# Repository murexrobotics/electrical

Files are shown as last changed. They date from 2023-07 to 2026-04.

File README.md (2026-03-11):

# MUREX Electrical

Attempt the impossible.

## Welcome!

Welcome to MUREX Robotics Electrical. We are focused on pushing boundaries and making electronics/systems design more accessible to all.

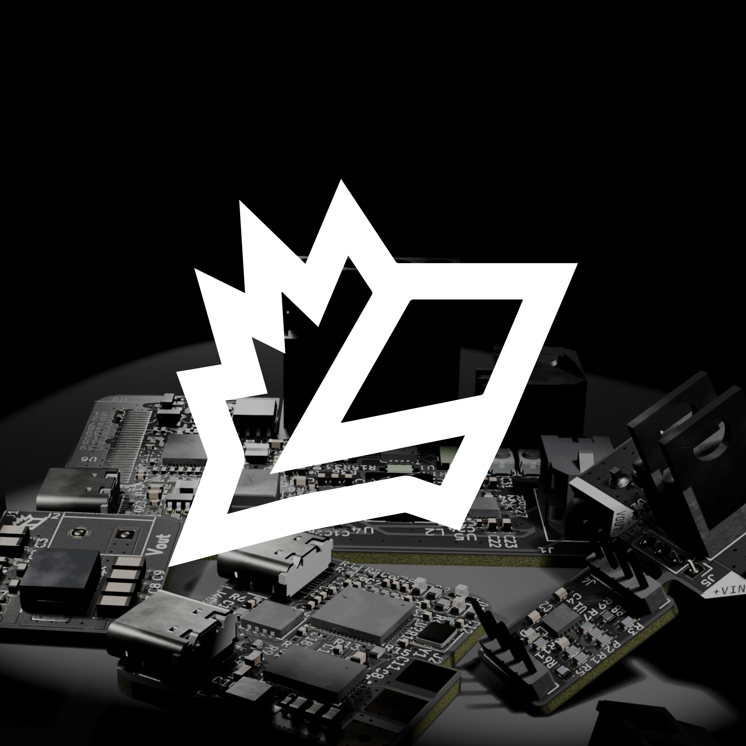
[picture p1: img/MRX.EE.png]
Cover Image


## Introduction

> *"I do not think there is any thrill that can go through the human heart like that felt by the inventor as he sees some creation of the brain unfolding to success"*
– [Nikola Tesla](https://en.wikipedia.org/wiki/Nikola_Tesla)

MUREX Robotics Electrical focuses on making everything highly integrated and custom. We make industrial/commercial level motion, power, communication, vision and wireless systems accessible to all. By making components fully custom, we can accomplish unprecedented levels of integration within MUREX robotics systems. By keeping COTS parts to a minimum, we vertically integrate all aspects of the robot, minimize space, and surprisingly, minimize cost. We don't do it the easy way. That's not what we believe in.

## Attempt the Impossible

Going to back our "mission statement"... (it's not really a mission statement, more a motivational quote)

> *Attempt the impossible*

What does this mean? Now that you have read through what MUREX Robotics Electrical (or *elec*) is all about and equipped with technical expertise, we can finally say what the true meaning is.

***Attempt the impossible***: We do it the best way possible. If pre-built parts or breakout boards don't cut it, we don't use it. If a processor isn't powerful enough, we don't use it. If a board isn't small enough, we make it smaller. No matter how difficult it may be to accomplish, we will follow through. No matter how hard it is. Things don't always go your way. No matter how hard you try to perfect your schematic, your PCB layout, your system integration, it still might not work out. Things are bound to go wrong, and it is up to *us* do it right. It's "impossible", a non-MUREX Robotics Electrical member might say. However, we accept it as the process. In the end, we will have achieved something others might have called "impossible". But the achievement only comes through endless, motivated attempts at the impossible.

> *Think Different*\
> *Unleash Innovation*\
> *Do It Right*

*Always attempting the impossible,*\
Members:

- Max Liu '26 (@xamuil2)
- Crane Lee '27 (@Crane-Lee)
- Osbert Chang '27 (@Osbertchang)
- Andrew Chen '28

Emeriti:

- Byran Huang '25 (@Hello9999901)
- Altan Unver '25 (@L0ad1n6)
- Varit Asavathiratham '25 (@BaritoDespacito)
- Chaney Hollis '23 (@chaneyhollis)

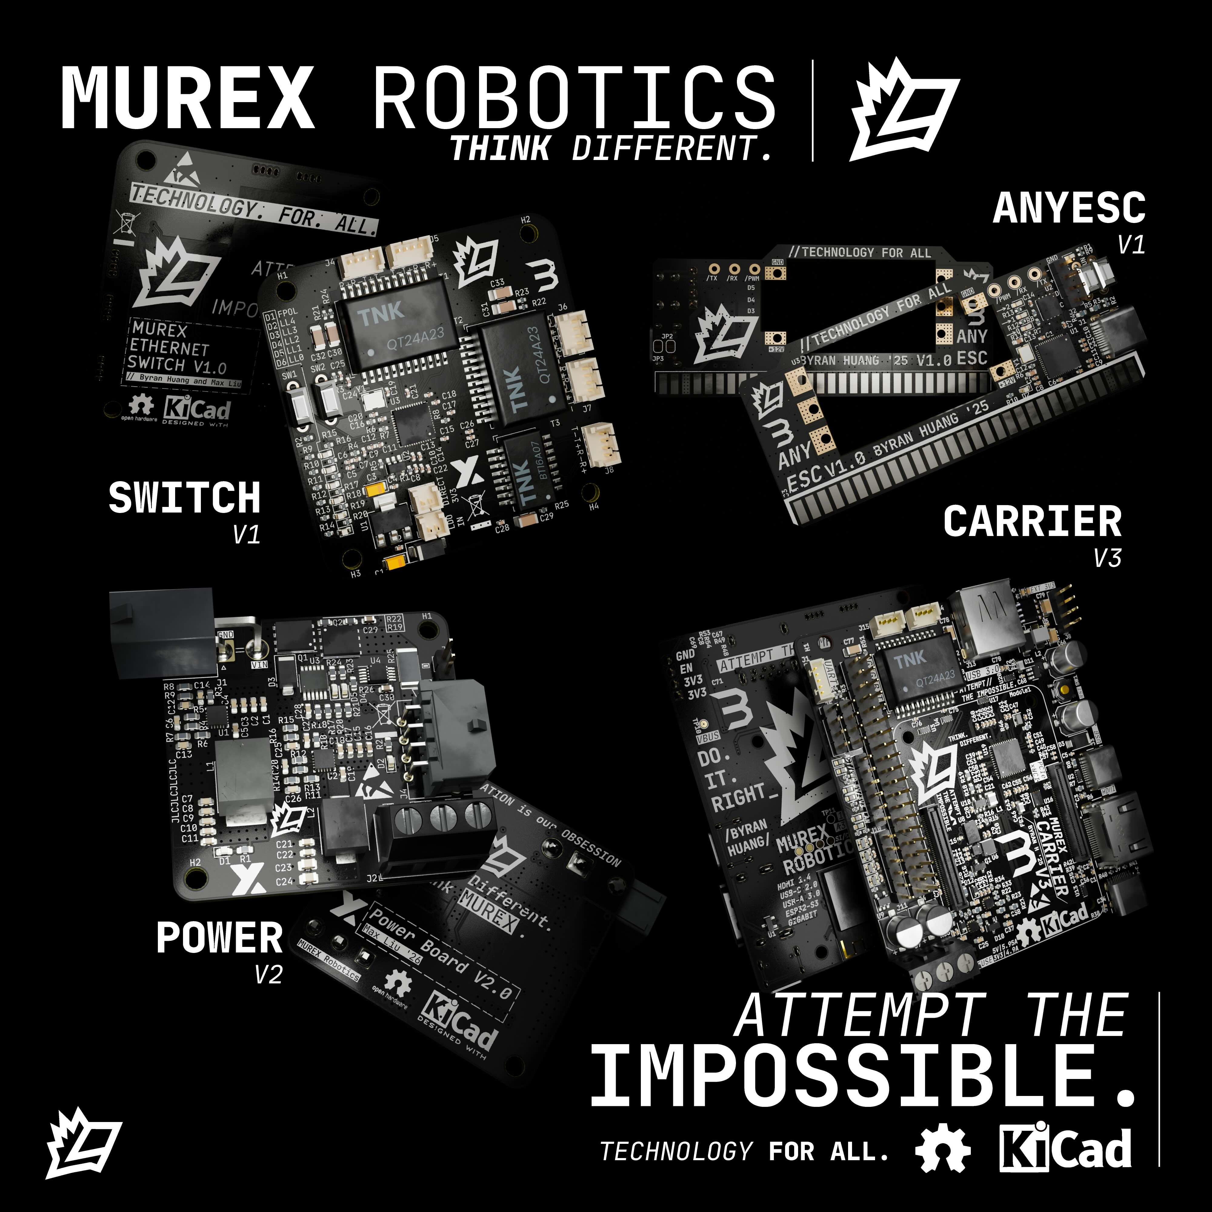
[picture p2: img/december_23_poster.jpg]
Raytraced Render

> December 2023 progress poster

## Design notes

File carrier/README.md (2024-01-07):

# Documentation

<https://docs.murexrobotics.com/elec/boards/carrier>

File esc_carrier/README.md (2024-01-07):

# Documentation

<https://docs.murexrobotics.com/elec/boards/esc_carrier>

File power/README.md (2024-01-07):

# Documentation

<https://docs.murexrobotics.com/elec/boards/power>

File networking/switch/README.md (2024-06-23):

# Documentation

<https://docs.murexrobotics.com/elec/boards/networking/switch>

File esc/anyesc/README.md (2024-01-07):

# Documentation

<https://docs.murexrobotics.com/elec/boards/esc>

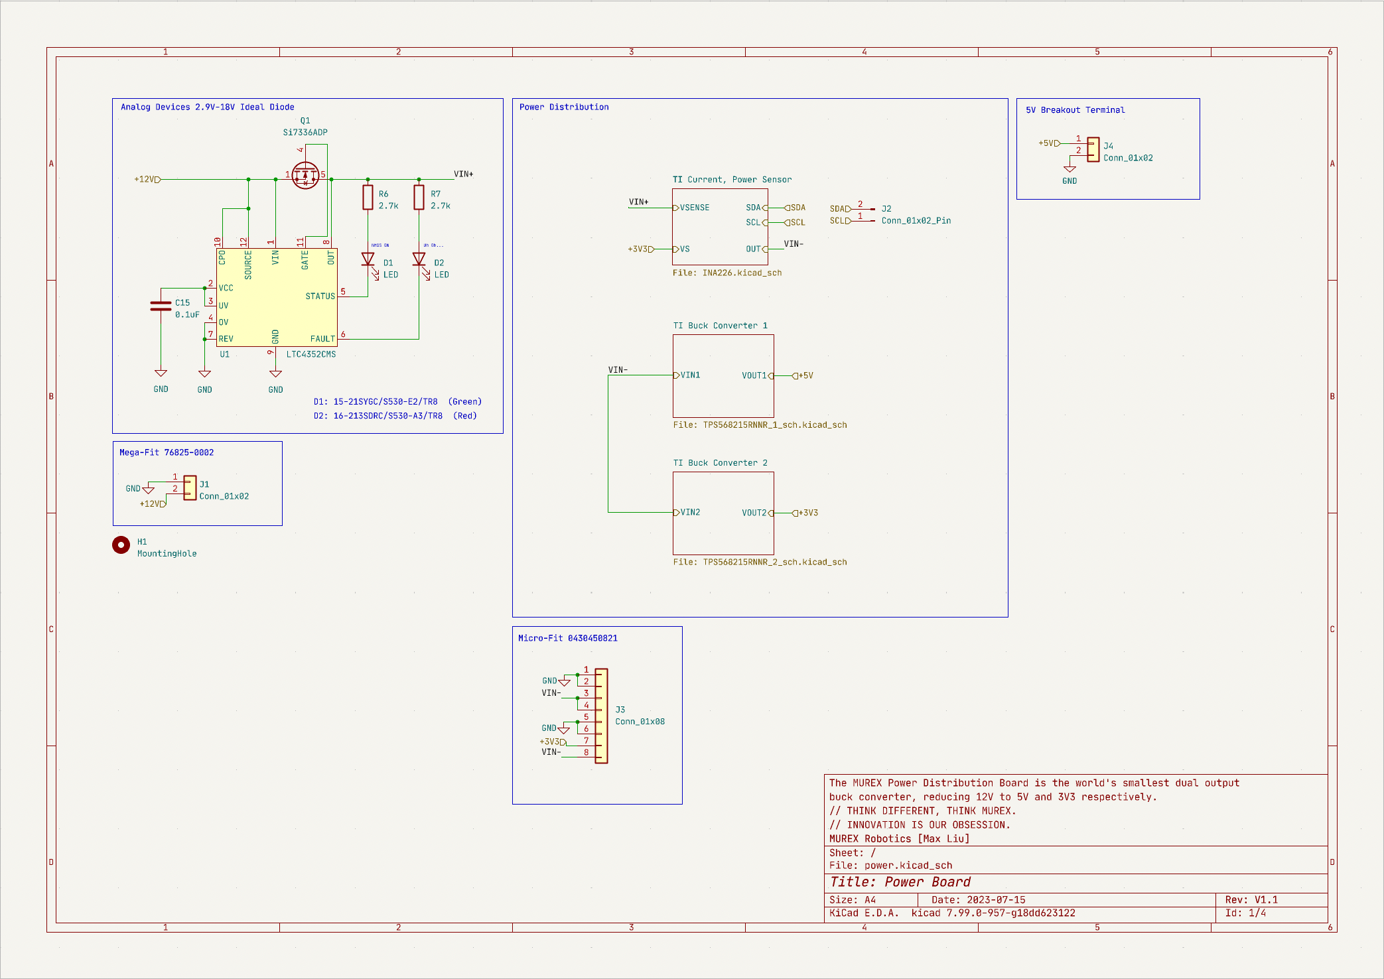
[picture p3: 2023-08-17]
power/power_board_schematic_preview.png

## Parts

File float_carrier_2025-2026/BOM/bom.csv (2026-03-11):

Comment | Designator | Footprint | LSCS Part Number
0.1uF | C5, C6 | C_0402_1005Metric | C141382
10uF | C1, C2 | C_0603_1608Metric | C694533
22uF | C3, C4, C7 | C_0603_1608Metric | C60077
LED | D1 | LED_0603_1608Metric | C2286
2.2uH | L1 | L_Bourns_SRP7028A_7.3x6.6mm | C2847539
10k | R1, R3, R4 | R_0603_1608Metric | C5123581
33.2k | R2 | R_0603_1608Metric | C23003
TPS563200 | U2 | SOT-23-6 | C97253

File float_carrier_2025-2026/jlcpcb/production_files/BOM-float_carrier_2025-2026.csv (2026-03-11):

Comment | Designator | Footprint | LCSC | Quantity
0.1uF | C5,C6 | C_0402_1005Metric | C1525 | 2
10k | R1,R3,R4 | R_0603_1608Metric | C25804 | 3
10uF | C1,C2 | C_0603_1608Metric | C19702 | 2
2.2uH | L1 | L_Bourns_SRP7028A_7.3x6.6mm | C2847539 | 1
22uF | C3,C4,C7 | C_0603_1608Metric | C59461 | 3
33.2k | R2 | R_0603_1608Metric | C4216 | 1
LED | D1 | LED_0603_1608Metric | C2286 | 1
TPS563200 | U2 | SOT-23-6 | C97253 | 1
Conn_01x07_Socket | J6 | PinSocket_1x07_P2.54mm_Vertical |  | 1
Screw_Terminal_01x02 | J7 | TerminalBlock_Xinya_XY308-2.54-2P_1x02_P2.54mm_Horizontal |  | 1
Conn_01x18_Socket | J1 | PinSocket_1x18_P2.54mm_Vertical |  | 1
Screw_Terminal_01x03_GND | J5 | TerminalBlock_Xinya_XY308-2.54-3P_1x03_P2.54mm_Horizontal |  | 1
Conn_01x18_Socket | J2 | PinSocket_1x18_P2.54mm_Vertical |  | 1
Screw_Terminal_01x03_Servo | J4 | TerminalBlock_Xinya_XY308-2.54-3P_1x03_P2.54mm_Horizontal |  | 1
Screw_Terminal_01x04_Depth_Sensor | J3 | TerminalBlock_Xinya_XY308-2.54-4P_1x04_P2.54mm_Horizontal |  | 1

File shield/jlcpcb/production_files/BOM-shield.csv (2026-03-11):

Comment | Designator | Footprint | LCSC
100nF | C1,C2,C4 | C_0603_1608Metric | C14663
SMDJ36A | D1 | D_SMC | C152051
LED | D2 | LED_0603_1608Metric | C2286
220k | R5 | R_0603_1608Metric | C22961
LED | D3 | LED_0603_1608Metric | C2297
3.3k | R10,R11,R3,R8 | R_0603_1608Metric | C22978
82k | R6,R9 | R_0603_1608Metric | C23254
100k | R4 | R_0603_1608Metric | C25803
18k | R7 | R_0603_1608Metric | C25810
22k | R1,R2 | R_0603_1608Metric | C31850
LM74810QDRRRQ1 | U1 | SON50P300X300X80-13N-D | C3215601
10nF | C3 | C_0603_1608Metric | C57112
47uF | C5 | C_1206_3216Metric | C76659

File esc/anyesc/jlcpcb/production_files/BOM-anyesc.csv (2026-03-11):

Comment | Designator | Footprint | LCSC
1k | R10,R11,R12,R13,R6,R7,R9 | R_0402_1005Metric | C11702
0.1uF | C1,C10,C2,C3,C4,C5,C6,C7,C8 | C_0402_1005Metric | C1525
30pF | C12,C13 | C_0603_1608Metric | C1658
USB_C_Receptacle_USB2.0 | J1 | USB_C_Receptacle_HRO_TYPE-C-31-M-12 | C165948
RP2040 | U1 | QFN-56-1EP_7x7mm_P0.4mm_EP3.2x3.2mm_ThermalVias | C2040
LED0 | D3 | LED_0603_1608Metric | C2286
LED | D1 | LED_0603_1608Metric | C2290
27 | R4,R5 | R_0603_1608Metric | C25190
10K | R1,R8 | R_0402_1005Metric | C25744
5.1k | R2,R3 | R_0402_1005Metric | C25905
W25Q64JVXGIQ | U2 | DFN_XGIQ TR_WIN-M | C2940195
1uF | C11,C14,C9 | C_0402_1005Metric | C52923
LED | D2 | LED_0603_1608Metric | C72038
LED1 | D4 | LED_0603_1608Metric | C72041
LED2 | D5 | LED_0603_1608Metric | C72043
12MHz | Y1 | Crystal_SMD_3225-4Pin_3.2x2.5mm | C9002
SW_Push | SW2 | SW_PUSH_6mm_SLIM
ESC Mount | H5 | Adjustable_ESC_Mount
ESC Mount | H4 | Adjustable_ESC_Mount
Conn_01x04 | J2 | PinHeader_1x04_P2.54mm_Vertical
B-G431B-ESC1 | U3 | B-G431B-ESC1_MOUNT
ESC_PWM | TP3 | TestPoint_THTPad_D2.5mm_Drill1.2mm
ESC_RX | TP2 | TestPoint_THTPad_D2.5mm_Drill1.2mm
5530843-7 | J3 | TE_5530843-7_PCB_Edge
ESC Mount | H6 | Adjustable_ESC_Mount
SW_Push | SW1 | SW_PUSH_6mm_SLIM
ESC_TX | TP1 | TestPoint_THTPad_D2.5mm_Drill1.2mm
RX | JP2 | SolderJumper-2_P1.3mm_Open_RoundedPad1.0x1.5mm
TX | JP3 | SolderJumper-2_P1.3mm_Open_RoundedPad1.0x1.5mm

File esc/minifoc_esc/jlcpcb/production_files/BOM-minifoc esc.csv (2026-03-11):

Comment | Designator | Footprint | LCSC
1k | R1,R2,R3,R4,R7,R9 | R_0402_1005Metric | C11702
2.7k | R12,R14,R15 | R_0603_1608Metric | C13167
47uH | L1 | SMNR3012-470MT | C135236
0.1uF | C1 | C_0603_1608Metric | C14663
0.1uF | C15,C16,C17,C18,C19,C20,C23,C24 | C_0402_1005Metric | C1525
27pF | C11,C12 | C_0402_1005Metric | C1557
30pF | C5,C6,C7 | C_0402_1005Metric | C1570
1uF | C3,C8,C9 | C_0603_1608Metric | C15849
RP2040 | U2 | QFN-56-1EP_7x7mm_P0.4mm_EP3.2x3.2mm | C2040
LED_Small | D3 | LED_0603_1608Metric | C2286
LED_Small | D2 | LED_0603_1608Metric | C2290
27 | R10,R11 | R_0402_1005Metric | C25156
10k | R13,R8 | R_0603_1608Metric | C25804
5.1k | R5,R6 | R_0402_1005Metric | C25905
USB_C_Receptacle_USB2.0_16P | J4,J6 | USB_C_Receptacle_HRO_TYPE-C-31-M-12 | C2927038
W25Q64JVXGIQ TR | U3 | DFN_XGIQ TR_WIN | C2940195
1uF | C13,C14,C21,C22 | C_0402_1005Metric | C52923
DRV8316CRRGFR | U1 | VQFN40_RGF_TEX-L | C5447274
22uF | C10 | C_0603_1608Metric | C59461
LED_Small | D1 | LED_0603_1608Metric | C72038
47nF | C4 | C_0402_1005Metric | C77012
12Mhz | Y1 | Crystal_SMD_3225-4Pin_3.2x2.5mm | C9002
10uF | C2 | C_0603_1608Metric | C96446
Conn_01x03 | J2 | ESC

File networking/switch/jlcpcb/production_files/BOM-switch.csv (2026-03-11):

Comment | Designator | Footprint | LCSC | Quantity
22uF | C11,C12,C6,C7 | C_0402_1005Metric | C105226 | 4
1k | R10,R11,R12,R13,R14,R9 | R_0402_1005Metric | C11702 | 6
0.1uF | C13,C14,C15,C16,C17,C18,C2,C21,C22,C23,C24,C25,C26,C27,C28,C4,C5,C9 | C_0402_1005Metric | C1525 | 18
10uF/NC | C10 | C_0402_1005Metric | C15525 | 1
30pF | C19,C20 | C_0603_1608Metric | C1658 | 2
0 | R1,R4,R7 | R_0402_1005Metric | C17168 | 3
BT16A07 | T3 | BT16A07 | C216355 | 1
QT48A03 | T2 | QT48A03 | C216365 | 1
~ | D3,D6 | LED_0603_1608Metric | C2286 | 2
~ | D2,D5 | LED_0603_1608Metric | C2290 | 2
4.7uF | C8 | C_0402_1005Metric | C23733 | 1
Input Diode | D7 | D_SMA | C2479 | 1
75 | R21,R22,R23,R24,R25 | R_0402_1005Metric | C25133 | 5
470K | R6 | R_0402_1005Metric | C25562 | 1
6.2k 1% | R8 | R_0402_1005Metric | C25915 | 1
25MHz | Y1 | Crystal_SMD_3225-4Pin_3.2x2.5mm | C337588 | 1
LM1117MP-3.3 | U1 | SOT-223-3_TabPin2 | C498153 | 1
10uF | C1,C3 | CP_EIA-3216-18_Kemet-A | C7171 | 2
~ | D1,D4 | LED_0603_1608Metric | C72038 | 2
IP175G | U3 | QFN-48-1EP_6x6mm_P0.4mm_EP4.3x4.3mm_ThermalVias | C80220 | 1
1nF 2KV (1206) | C29,C30,C31,C32,C33 | C_1206_3216Metric | C9196 | 5
PHY 1 | J8 | Molex_PicoBlade_53047-0410_1x04_P1.25mm_Vertical |  | 1
PHY 3 | J6 | Molex_PicoBlade_53047-0410_1x04_P1.25mm_Vertical |  | 1
MountingHole | H1 | MountingHole_3.2mm_M3 |  | 1
PHY 5 | J4 | Molex_PicoBlade_53047-0410_1x04_P1.25mm_Vertical |  | 1
MountingHole | H2 | MountingHole_3.2mm_M3 |  | 1
LDO IN | J1 | Molex_PicoBlade_53047-0210_1x02_P1.25mm_Vertical |  | 1
PHY 2 | J7 | Molex_PicoBlade_53047-0410_1x04_P1.25mm_Vertical |  | 1
3.3V IN | J3 | Molex_PicoBlade_53047-0210_1x02_P1.25mm_Vertical |  | 1
PHY 4 | J5 | Molex_PicoBlade_53047-0410_1x04_P1.25mm_Vertical |  | 1

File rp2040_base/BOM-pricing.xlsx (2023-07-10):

Value | Footprint | Quantity | Unit Price | Component Total | JLC Extended | Assembly Quantity | JLC Total: | JLC Unit Price: | XIAO Unit Price | Pico Unit Price
1kΩ | 0402 | 2 | $0.0005 | $0.00100 | $0.00 | 1 | $16.40100 | $16.40100 | $5.40 | $4.00
0.1uF | 0402 | 9 | $0.0008 | $0.00720 | $0.00 | 5 | $22.00500 | $4.40100 | $5.40 | $4.00
27pF | 0402 | 2 | $0.0010 | $0.00200 | $0.00 | 10 | $29.01000 | $2.90100 | $5.40 | $4.00
USB-C | USB-C | 1 | $0.2007 | $0.20070 | $3.00 | 15 | $36.01500 | $2.40100 | $5.40 | $4.00
RP2040 | QFN-56 | 1 | $0.9761 | $0.97610 | $3.00 | 20 | $43.02000 | $2.15100 | $5.40 | $4.00
27Ω | 0603 | 2 | $0.0009 | $0.00180 | $0.00 | 25 | $50.02500 | $2.00100 | $5.40 | $4.00
10kΩ | 0402 | 2 | $0.0005 | $0.00100 | $0.00 | 30 | $57.03000 | $1.90100 | $5.40 | $4.00
5.1kΩ | 0402 | 2 | $0.0005 | $0.00100 | $0.00 | 35 | $64.03500 | $1.82957 | $5.40 | $4.00
12MHz | 2016 | 1 | $0.0765 | $0.07650 | $3.00 | 40 | $71.04000 | $1.77600 | $5.40 | $4.00
W25Q64JVXGIQ | XSON-8 | 1 | $0.0765 | $0.07650 | $3.00 | 45 | $78.04500 | $1.73433 | $5.40 | $4.00
1uF | 0402 | 3 | $0.0038 | $0.01140 | $0.00 | 50 | $85.05000 | $1.70100 | $5.40 | $4.00
WS2128B | 5050 | 1 | $0.0458 | $0.04580 | $3.00

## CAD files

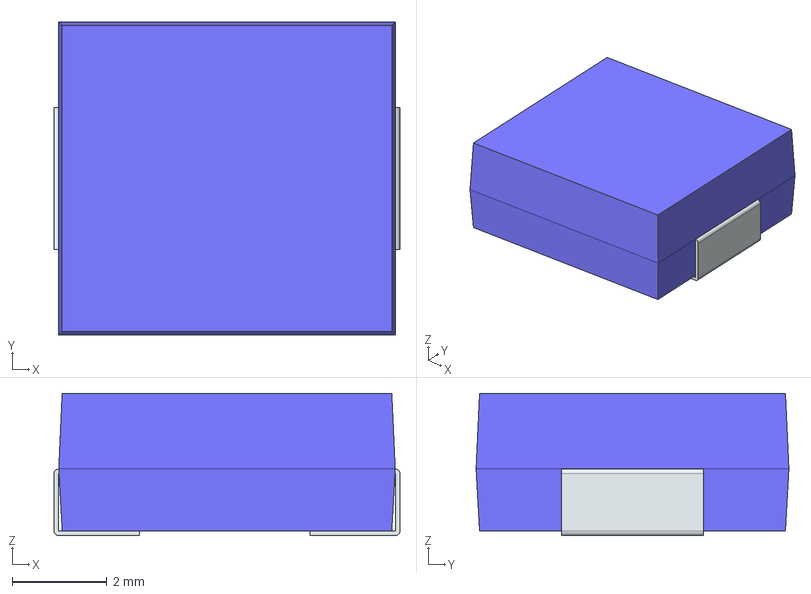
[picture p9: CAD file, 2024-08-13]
power2/LIB_SRP7028A-1R8M/SRP7028A-1R8M/3D/SRP7028A-1R8M.stp
7.30 x 6.60 x 3.00 mm
FilletPin1
FilletPin2

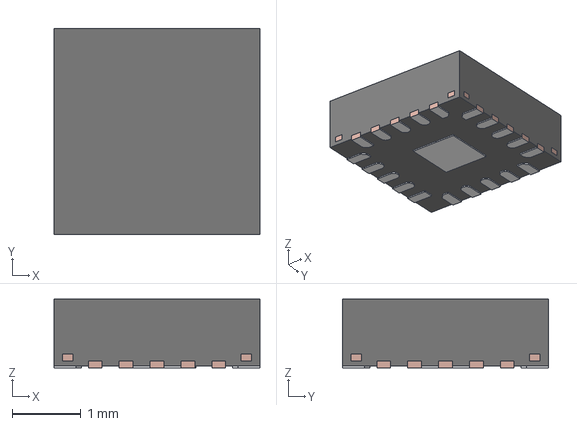
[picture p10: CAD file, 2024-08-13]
power2/LIB_TPS56C230RJER-2/TPS56C230RJER/3D/TPS56C230RJER.stp
3.00 x 3.00 x 1.00 mm
FRAME

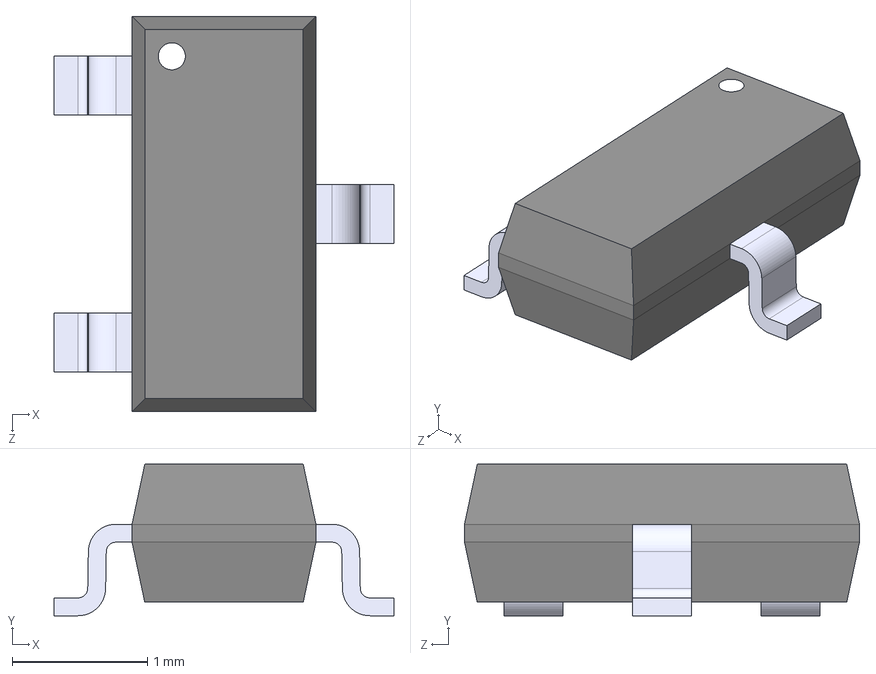
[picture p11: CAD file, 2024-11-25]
Smart Power Board/SPB_Library/FDN335N/FDN335N.step
2.51 x 1.12 x 2.92 mm

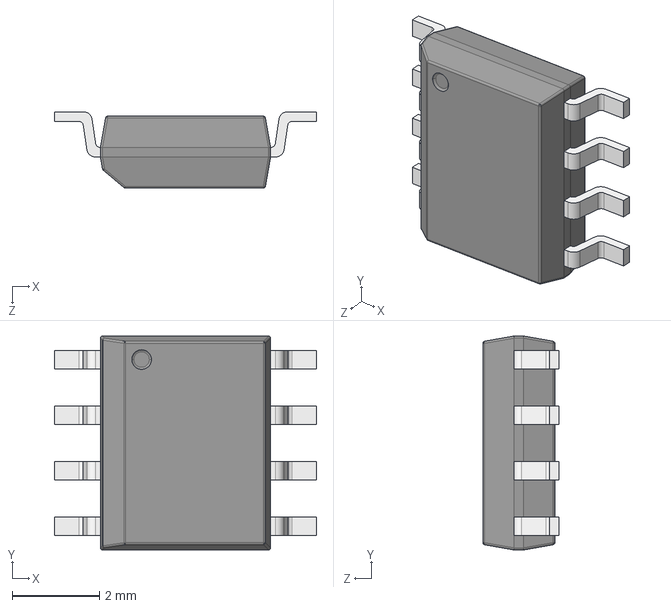
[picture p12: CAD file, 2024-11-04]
Smart Power Board/SPB_Library/LIB_FDS6690A/FDS6690A/3D/FDS6690A.stp
6.00 x 4.90 x 1.75 mm
pins

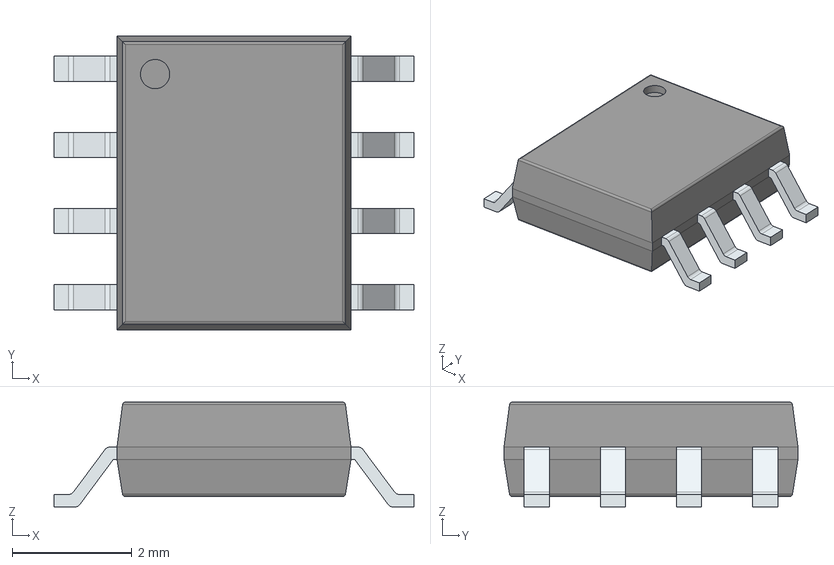
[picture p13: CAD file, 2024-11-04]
Smart Power Board/SPB_Library/LIB_IRF7416TRPBF/IRF7416TRPBF/3D/IRF7416TRPBF.stp
6.00 x 4.90 x 1.75 mm
PinsArrayLR

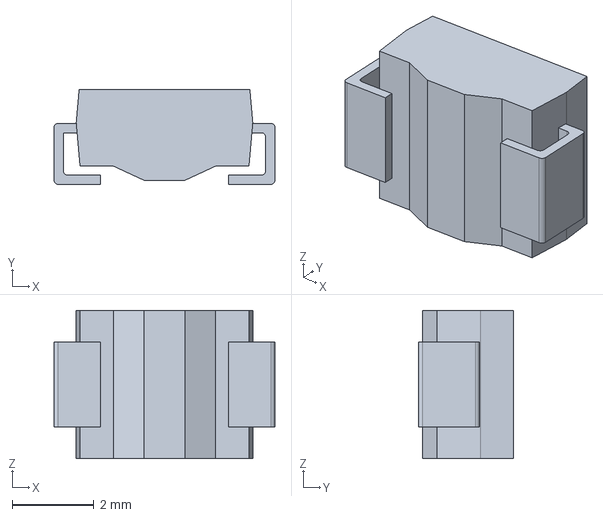
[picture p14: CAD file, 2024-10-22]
Smart Power Board/SPB_Library/LIB_SMBJ33CA/SMBJ33CA/3D/SMBJ33CA.stp
5.40 x 2.31 x 3.62 mm

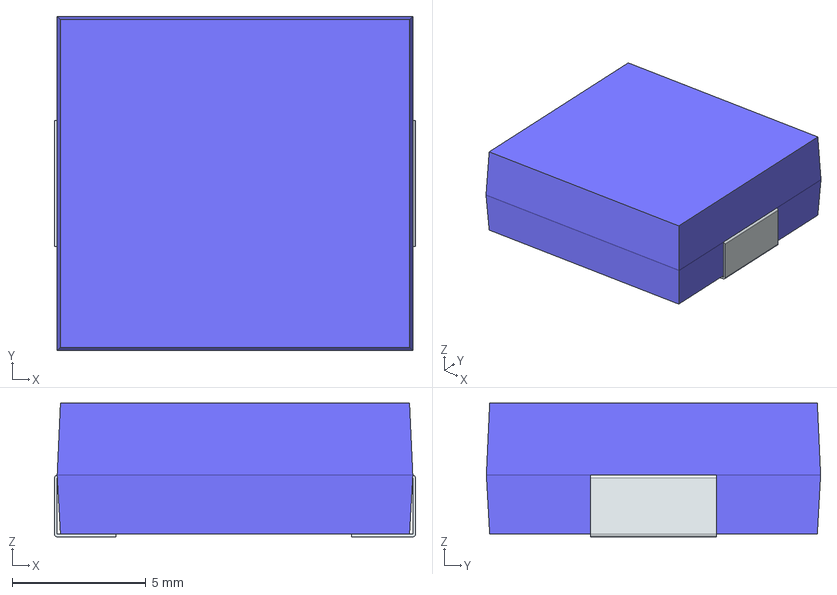
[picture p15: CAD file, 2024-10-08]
Smart Power Board/SPB_Library/LIB_SRP1245CC-1R5M/SRP1245CC-1R5M/3D/SRP1245CC-1R5M.stp
13.5 x 12.5 x 5.00 mm
FilletPin1
FilletPin2

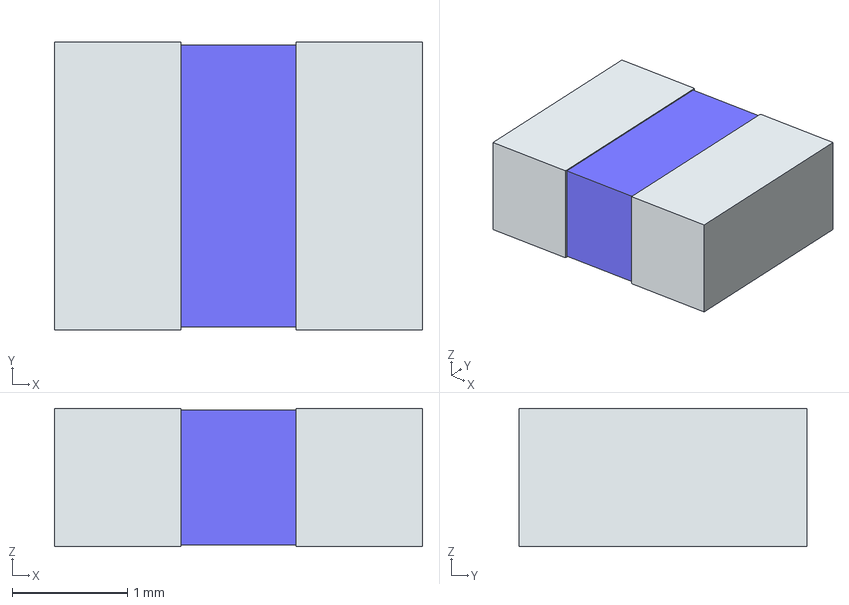
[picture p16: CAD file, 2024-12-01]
Smart Power Board/SPB_Library/LIB_SRP3212A-4R7M/SRP3212A-4R7M/3D/SRP3212A-4R7M.stp
3.20 x 2.50 x 1.20 mm
term1
term2

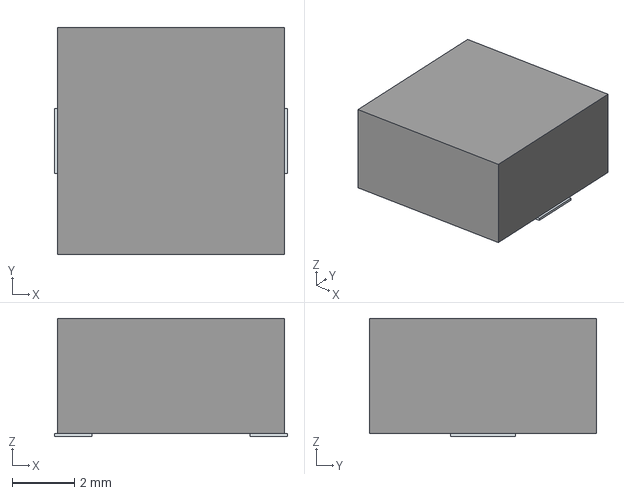
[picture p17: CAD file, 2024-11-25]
Smart Power Board/SPB_Library/LIB_SRR0735HA-151M/SRR0735HA-151M/3D/SRR0735HA-151M.stp
7.50 x 7.30 x 3.80 mm
Pins

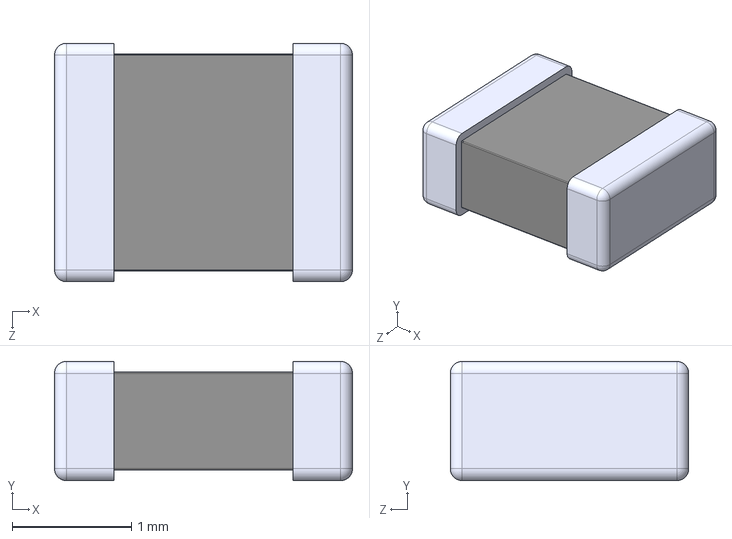
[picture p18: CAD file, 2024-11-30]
Smart Power Board/SPB_Library/MLP2520S3R3ST0S1/MLP2520S3R3ST0S1.step
2.50 x 1.00 x 2.00 mm

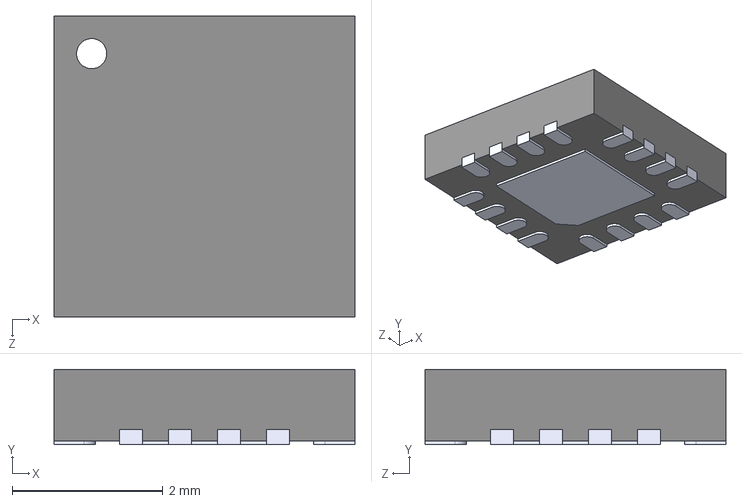
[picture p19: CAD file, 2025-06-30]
Smart Power Board/SPB_Library/INA3221AQRGVRQ1.STEP
4.00 x 1.00 x 4.00 mm

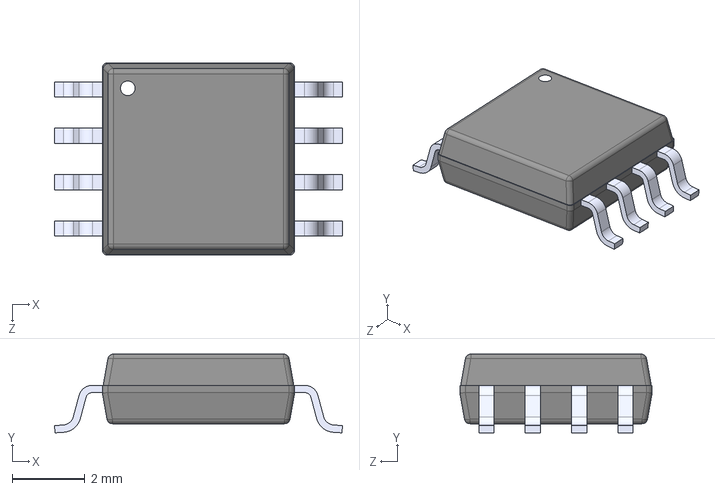
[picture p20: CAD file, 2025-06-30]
Smart Power Board/SPB_Library/W25Q32JVSSIQ--3DModel-STEP-269445.STEP
7.90 x 2.16 x 5.28 mm

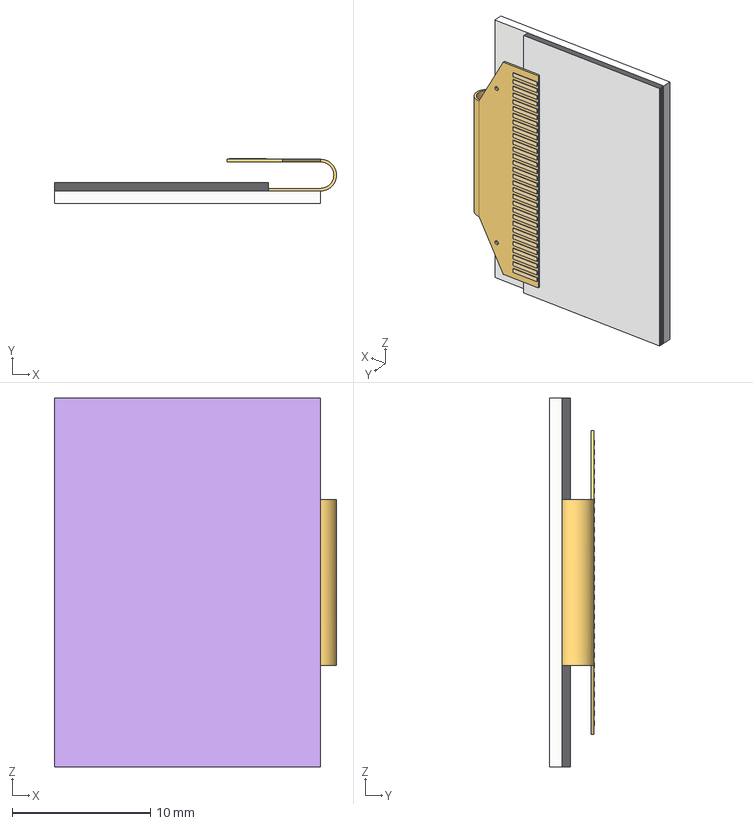
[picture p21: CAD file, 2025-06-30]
Smart Power Board/SPB_Library/OLED 128x64 ug-2864hsweg01 v15.igs
20.4 x 3.25 x 26.7 mm

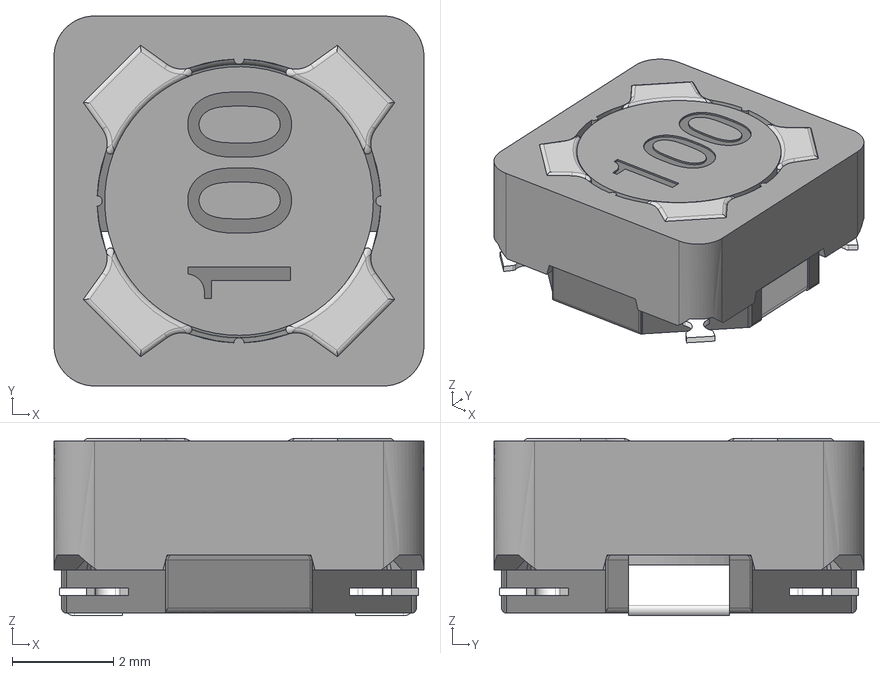
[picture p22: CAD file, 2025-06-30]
Smart Power Board/SPB_Library/SRR0735A.STP
7.30 x 7.30 x 3.50 mm

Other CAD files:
Smart Power Board/SPB_Library/LIB_MAX7500MSA+T/MAX7500MSA+T/3D/MAX7500MSA+T.stp
Smart Power Board/SPB_Library/SKRKAE.STEP
Smart Power Board/SPB_Library/0430450601.stp
Smart Power Board/SPB_Library/430450200.stp
Smart Power Board/SPB_Library/430450400/430450400.step
Smart Power Board/SPB_Library/430450601/430450601.step
Smart Power Board/SPB_Library/FL1200138/FL1200138.step
Smart Power Board/SPB_Library/LIB_282857-4/282857-4/3D/282857-4.stp
Smart Power Board/SPB_Library/LIB_282857-4/282857-4/Allegro/2828574.psm
Smart Power Board/SPB_Library/LIB_282857-4/282857-4/DEHDL/282857_4/chips/chips.prt
Smart Power Board/SPB_Library/LIB_FDS6690A/FDS6690A/Allegro/soic127p600x175-8n.psm
Smart Power Board/SPB_Library/LIB_FDS6690A/FDS6690A/DEHDL/fds6690a/chips/chips.prt
Smart Power Board/SPB_Library/LIB_IRF7416TRPBF/IRF7416TRPBF/Allegro/soic127p600x175-8n.psm
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

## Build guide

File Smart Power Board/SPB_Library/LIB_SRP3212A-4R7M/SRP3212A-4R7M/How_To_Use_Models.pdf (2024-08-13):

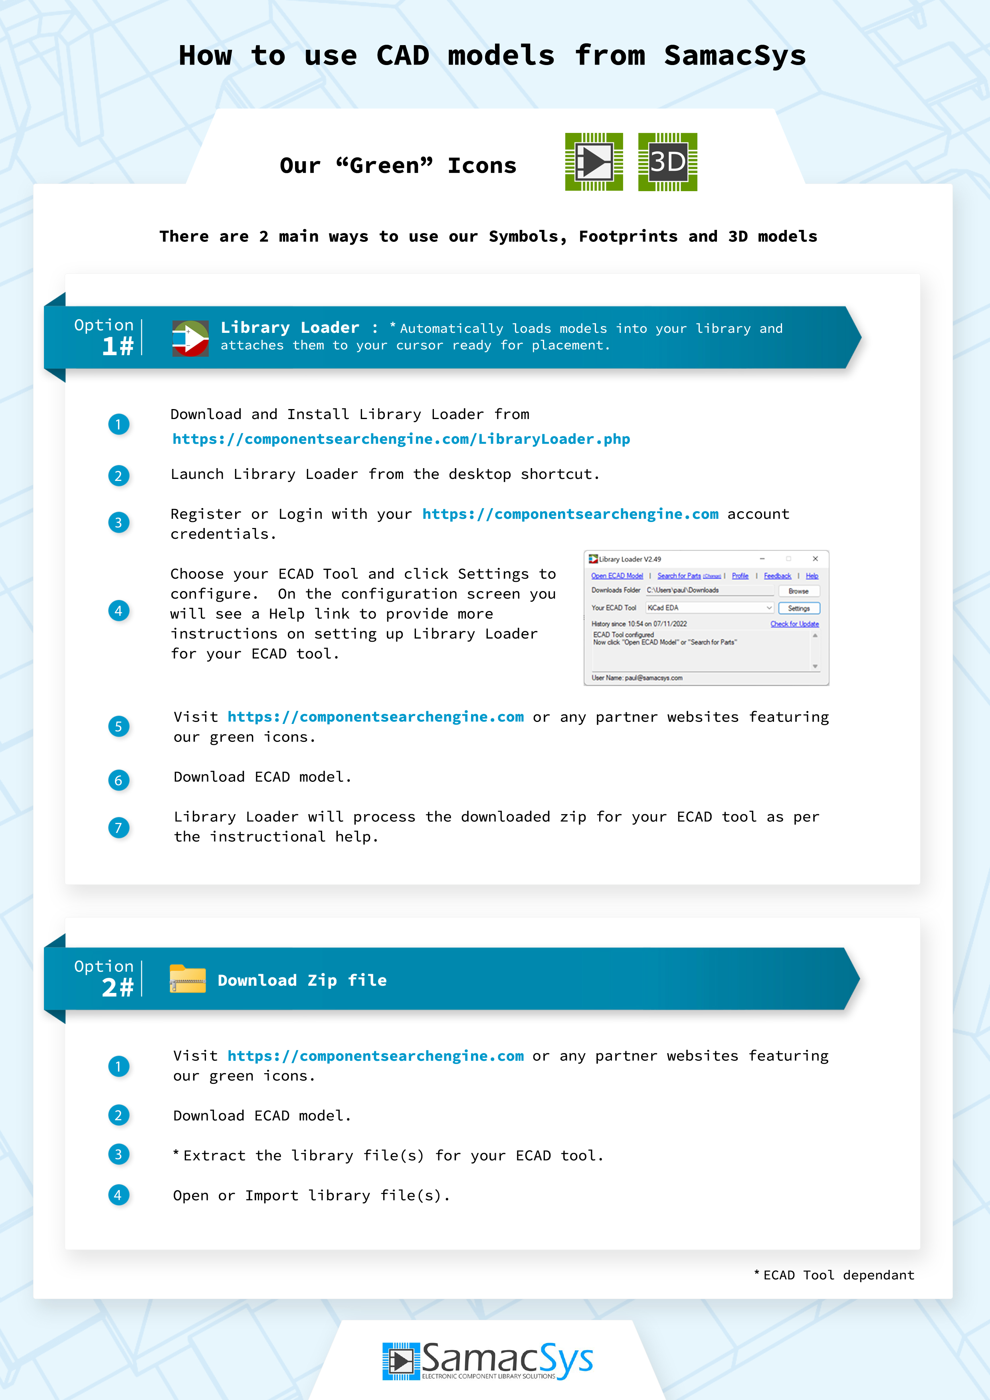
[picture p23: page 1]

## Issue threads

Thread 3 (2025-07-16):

BOM of Switch Ethernet

pcbkal, 2025-07-16:
When I saw your project it was really fascinating and I was amazed of your work and detection to this project ! a switch Ethernet as small as you PCB and  with 4 port is what I was looking for, I did printed a the PCB in JLC and I was missing the file of the BOM  that is why I couldn't add the file to the Fabrication! Would you mind add the BOM of this PCB! so I can test it ! and is there any problem if I edit the Design to match some specification i wold like to add ?

Closed 2025-07-16.

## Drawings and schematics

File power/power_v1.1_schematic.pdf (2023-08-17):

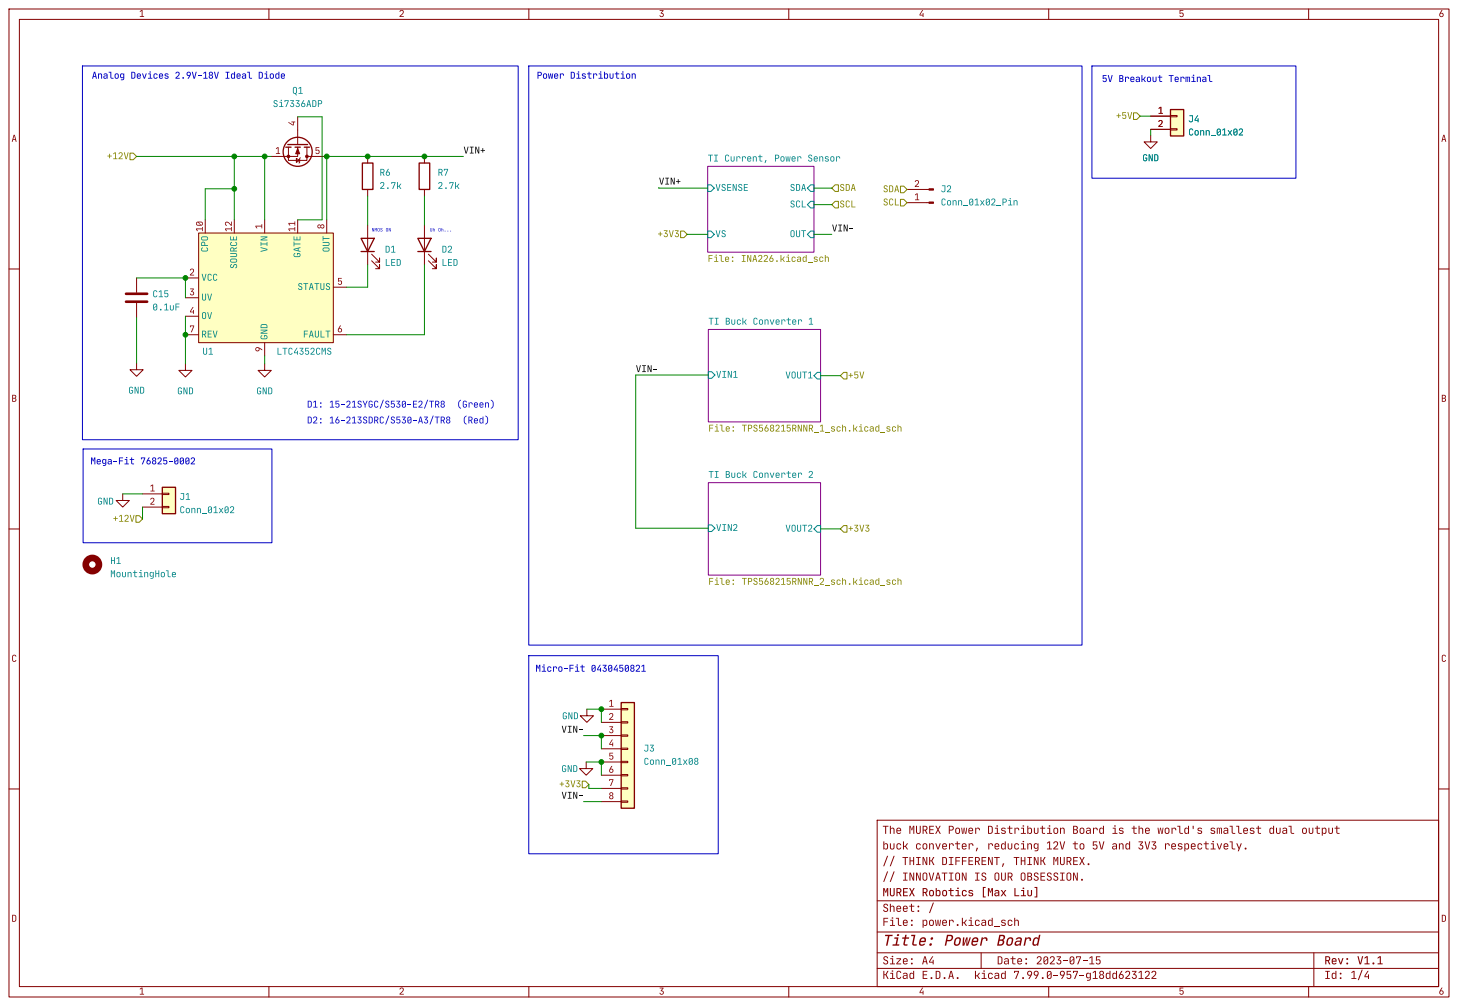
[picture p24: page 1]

// INNOVATION IS OUR OBSESSION.

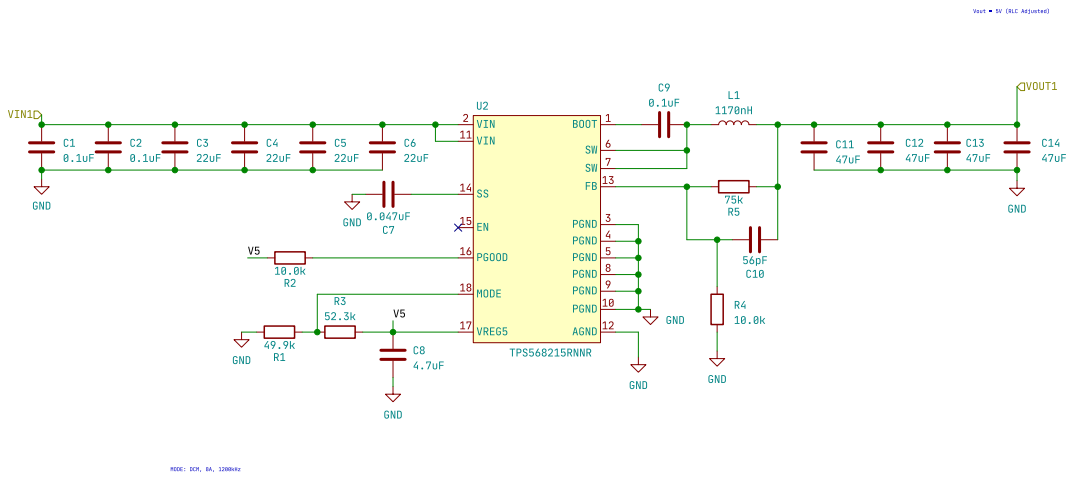
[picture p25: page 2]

Vout = 5V (RLC Adjusted) MODE: DCM, 8A, 1200kHz

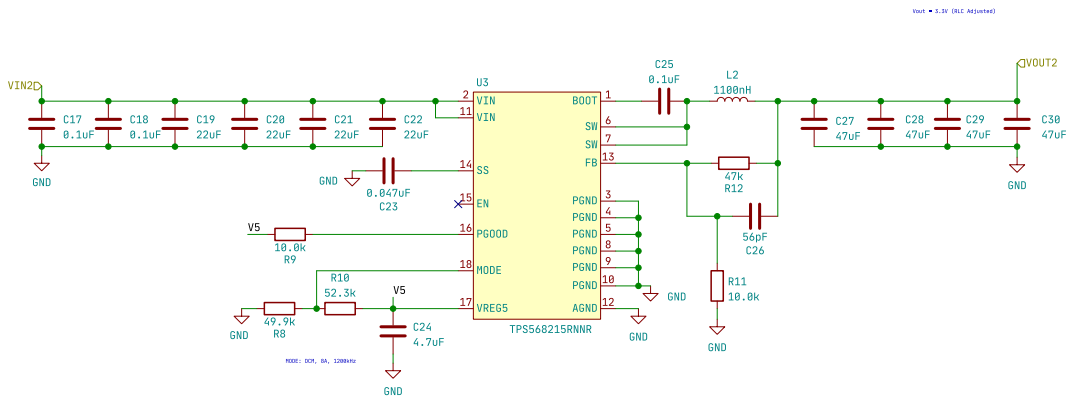
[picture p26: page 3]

Vout = 3.3V (RLC Adjusted) MODE: DCM, 8A, 1200kHz

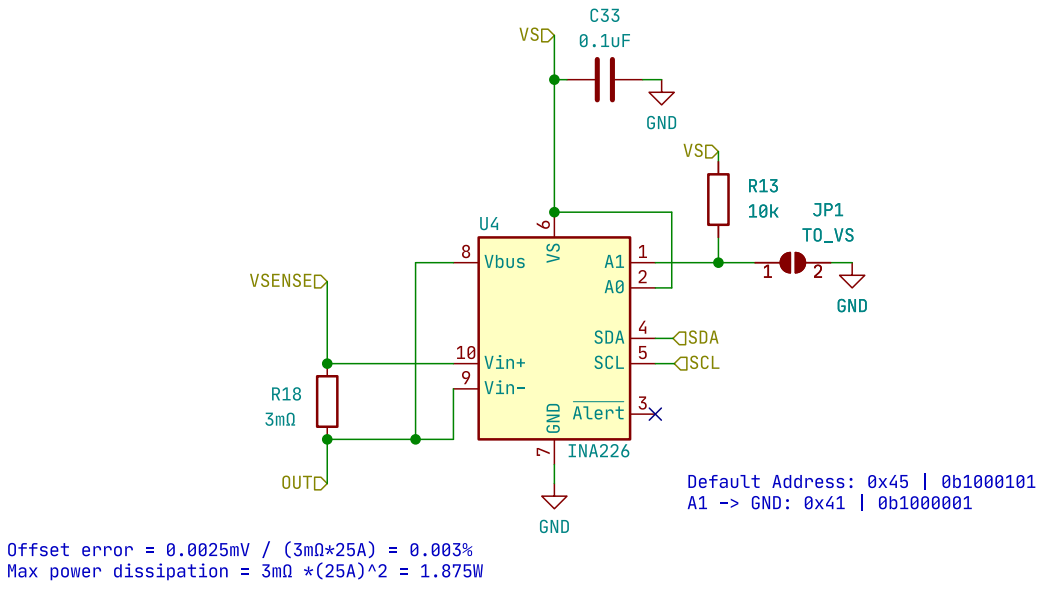
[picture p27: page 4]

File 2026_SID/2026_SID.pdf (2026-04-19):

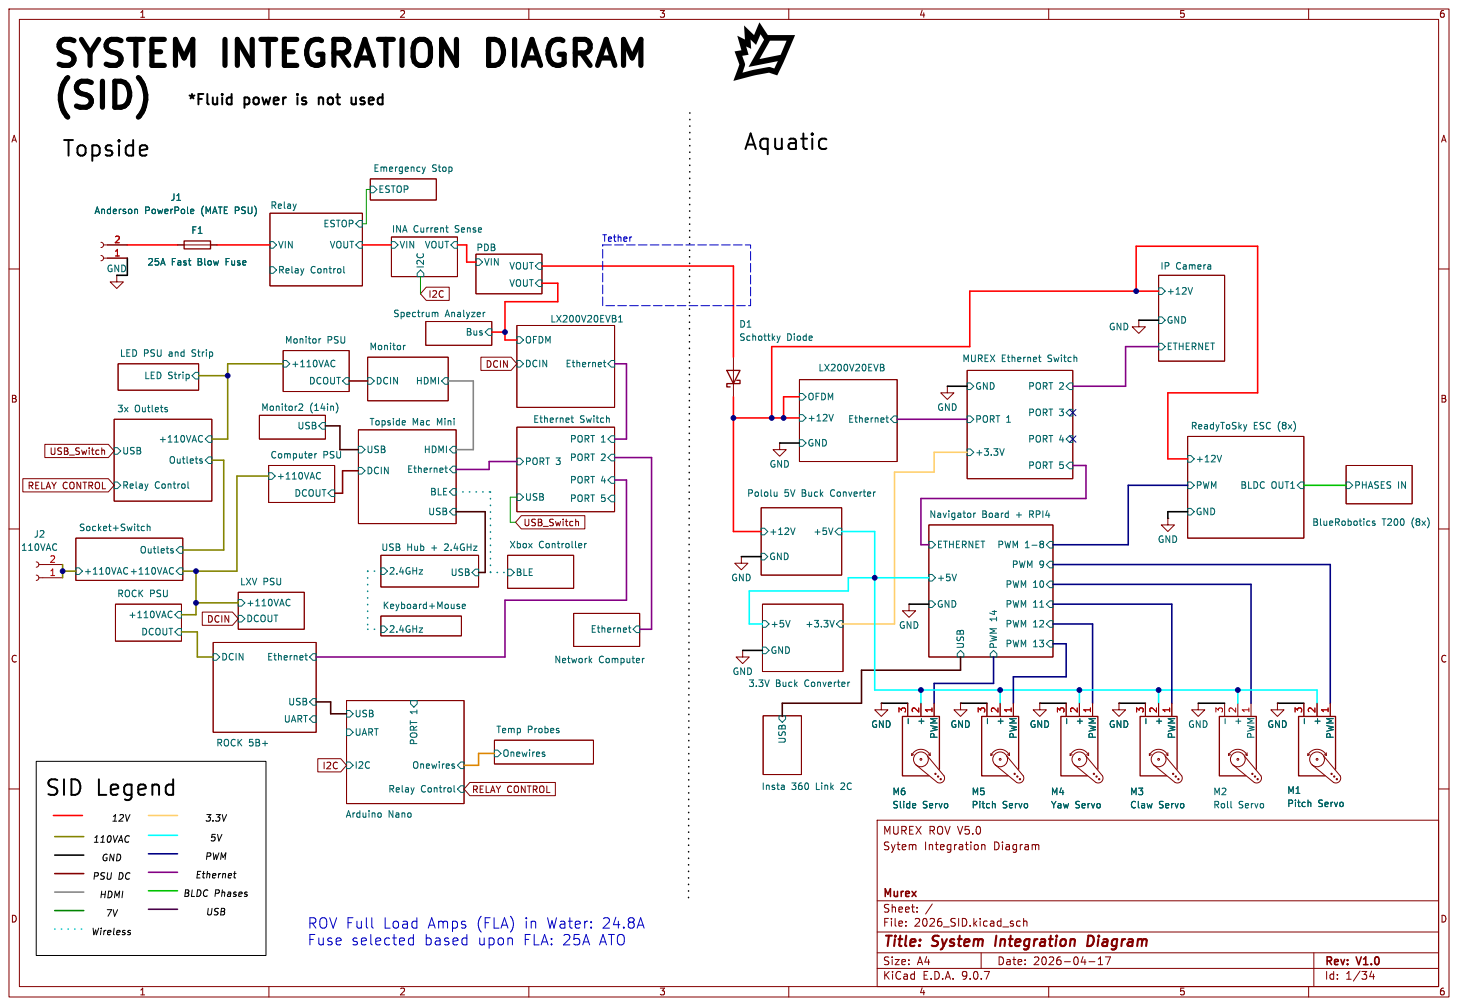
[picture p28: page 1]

J1 Anderson PowerPole (MATE PSU) 1

- 3 M6 Slide Servo GND GND GND

BLE HDMI Ethernet USB

- 3 M5 Pitch Servo GND GND PWM

- 3 M2 Roll Servo GND GND GND GND PWM

- 3 M3 Claw Servo GND GND PWM

BLDC Phases Ethernet 12V SID Legend

Fuse selected based upon FLA: 25A ATO

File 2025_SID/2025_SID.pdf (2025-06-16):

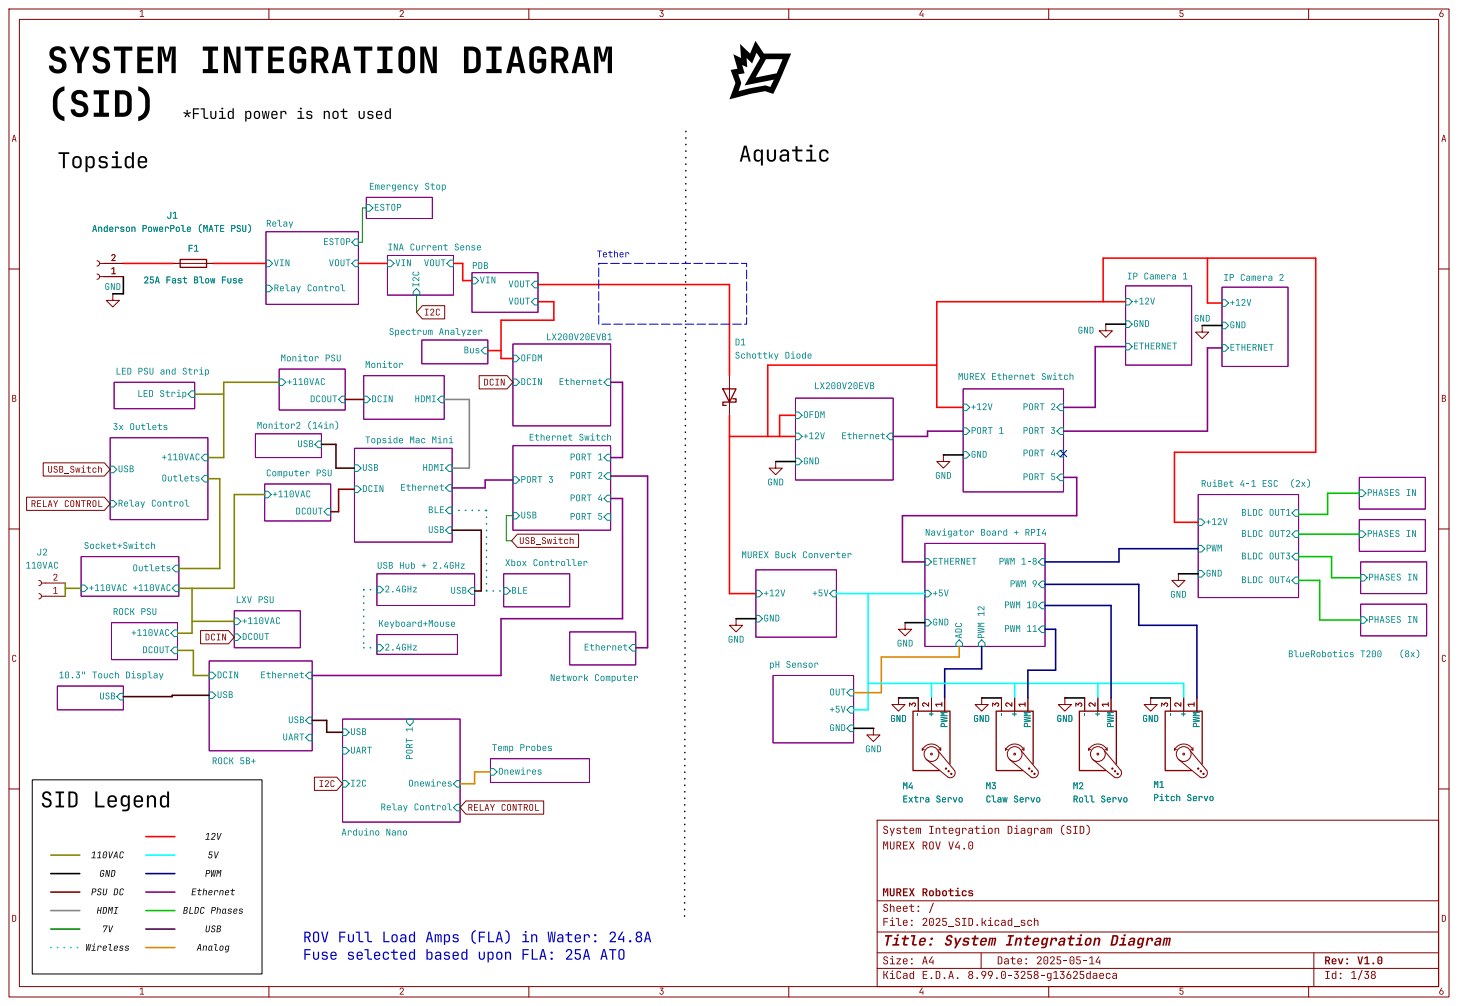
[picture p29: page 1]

J1 Anderson PowerPole (MATE PSU) 1

- 3 M1 Pitch Servo D1Schottky Diode GND

LED PSU and Strip Outlets USB
Topside Mac Mini LED Strip

BLE HDMI Ethernet USB

BLDC OUT1 BLDC OUT3 BLDC OUT4 PWM

Xbox Controller USB UART DCIN

Ethernet Network Computer BLE

- 3 M4 Extra Servo PWM GND

Analog BLDC Phases 7V SID Legend

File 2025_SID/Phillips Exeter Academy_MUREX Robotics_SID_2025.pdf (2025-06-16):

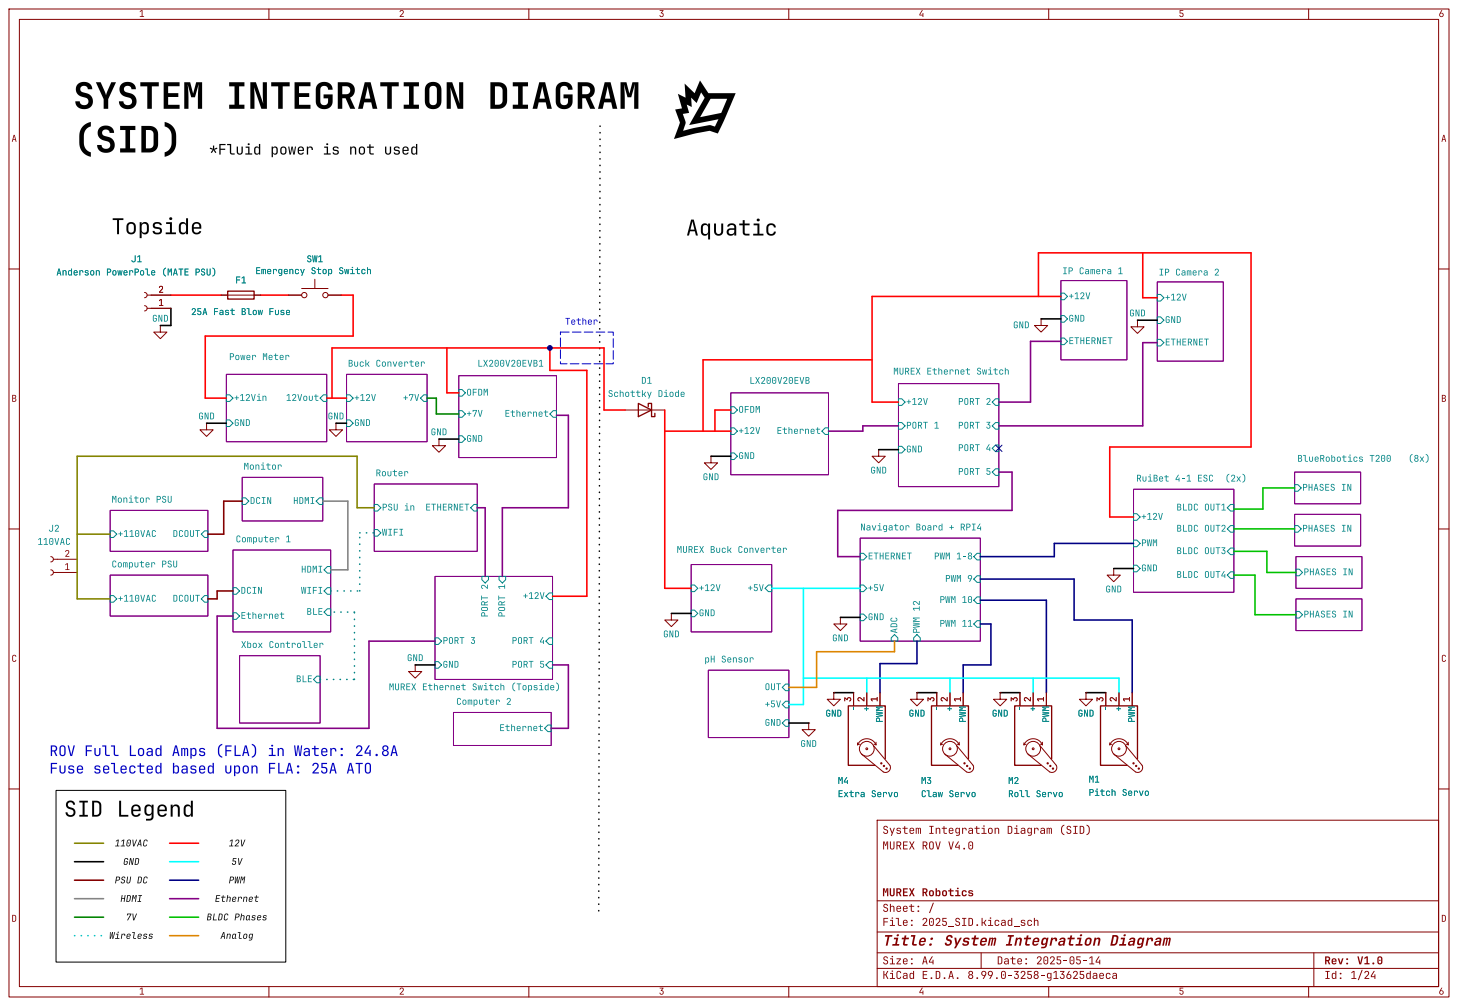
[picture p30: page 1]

- 3 M3 Claw Servo GND GND GND GND GND GND GND GND GND GND GND GND Topside

J1 Anderson PowerPole (MATE PSU) 1

BLDC OUT1 BLDC OUT3 BLDC OUT4 PWM

- 3 M1 Pitch Servo GND GND GND GND

- 3 GND GND GND M4 Extra ServoPWM1 +

Ethernet 7V Wireless ROV Full Load Amps (FLA) in Water: 24.8A
12V SID Legend

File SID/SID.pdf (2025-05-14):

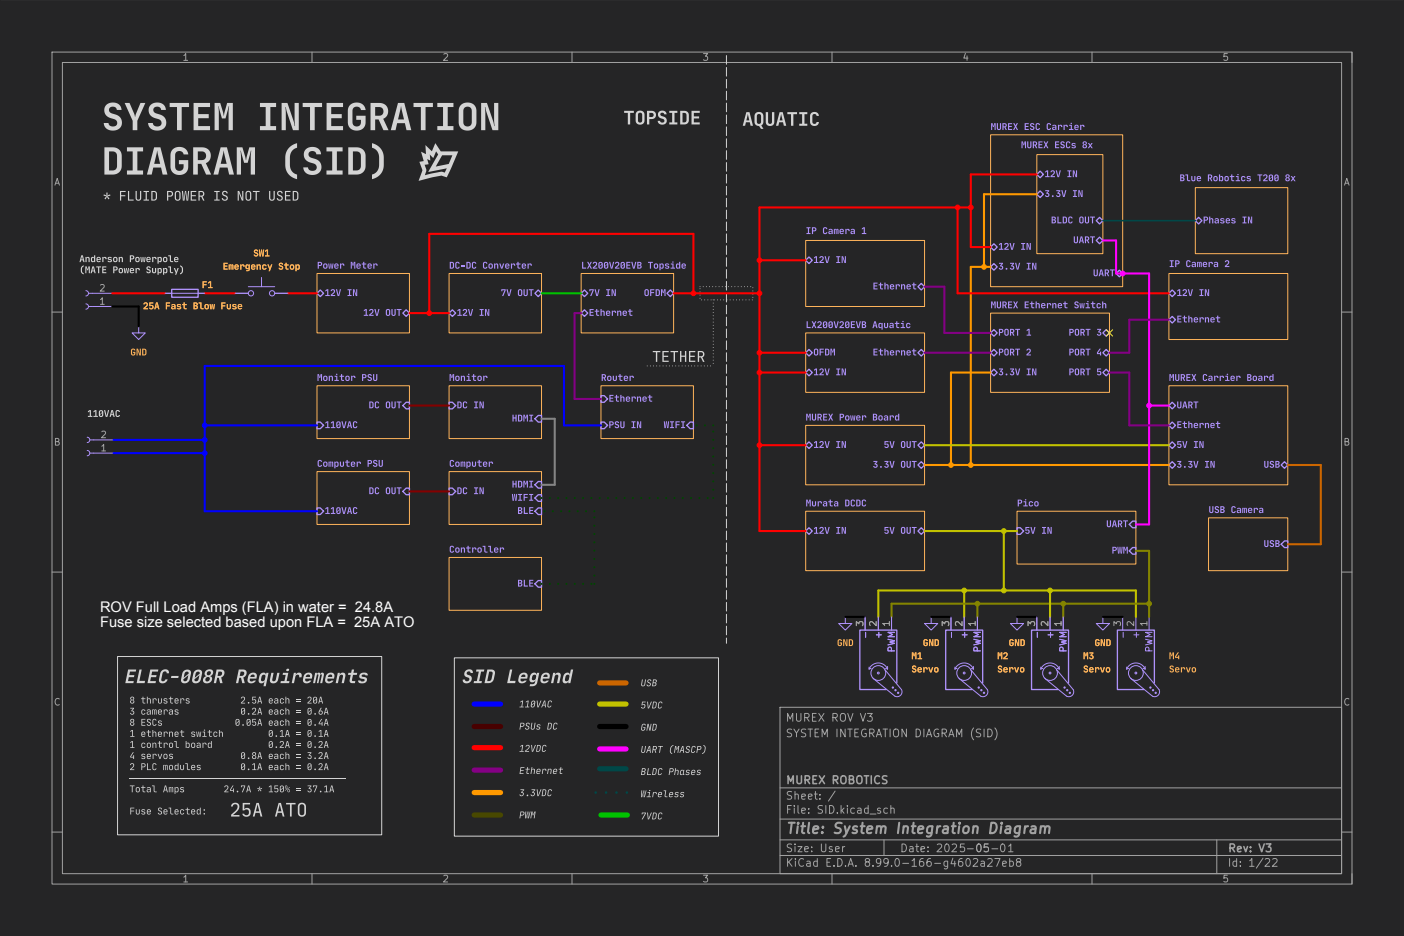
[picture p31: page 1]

SYSTEMINTEGRATION
7V OUT DC-DC Converter DC IN

IP Camera 2 Phases IN

- 3 M4 Servo GND GND PWM

DC OUT Monitor PSU

DC OUT Computer PSU

ROV Full Load Amps (FLA) in water = 24.8A
Fuse size selected based upon FLA = 25A ATO

UART (MASCP) BLDC Phases Wireless 7VDC

File: SID.kicad_sch Sheet: / MUREX ROBOTICS

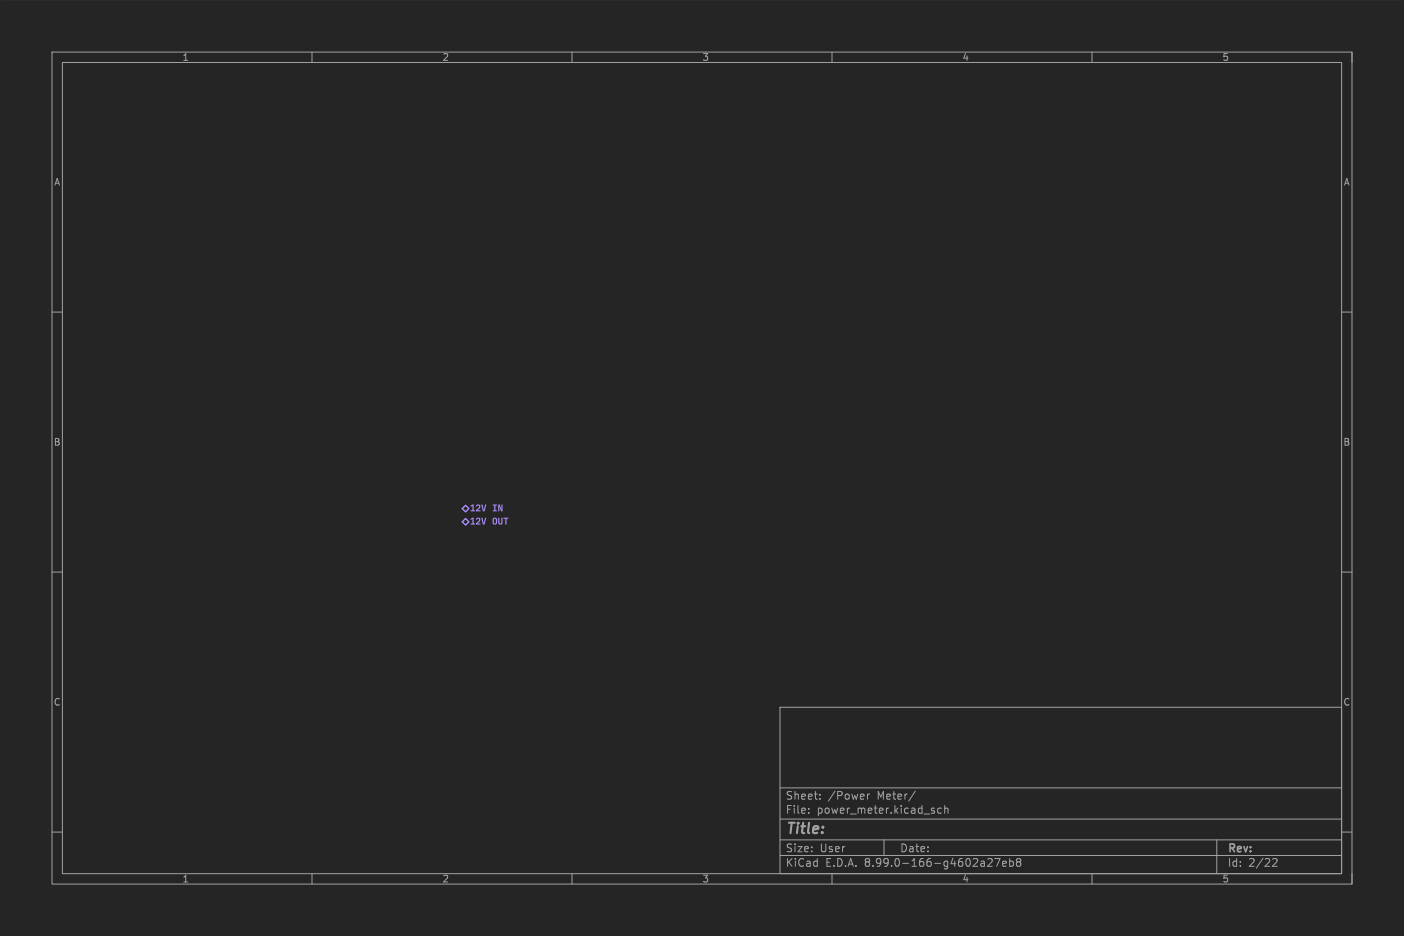
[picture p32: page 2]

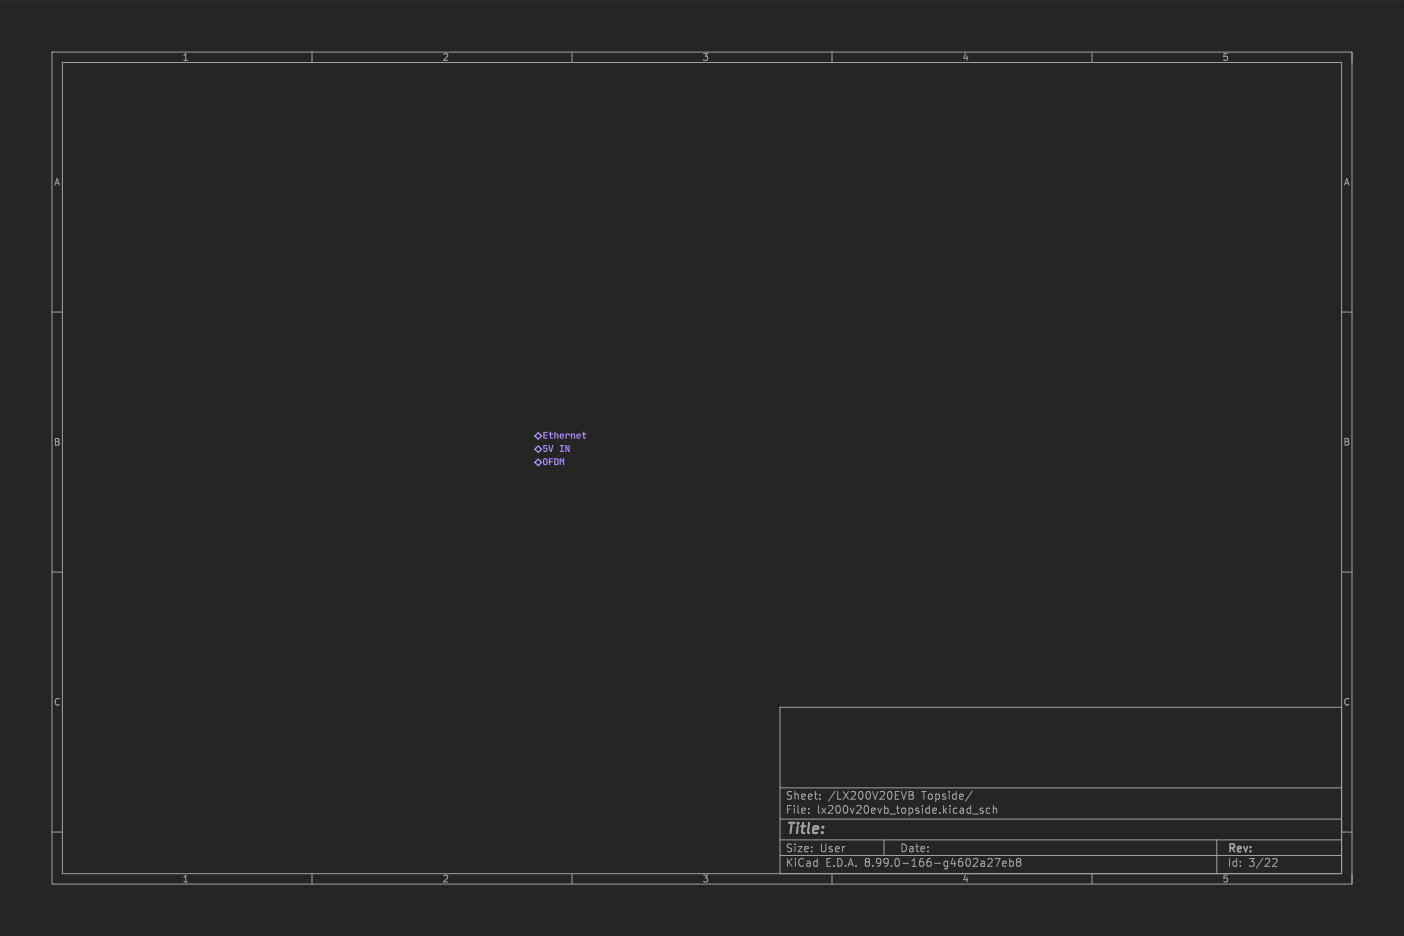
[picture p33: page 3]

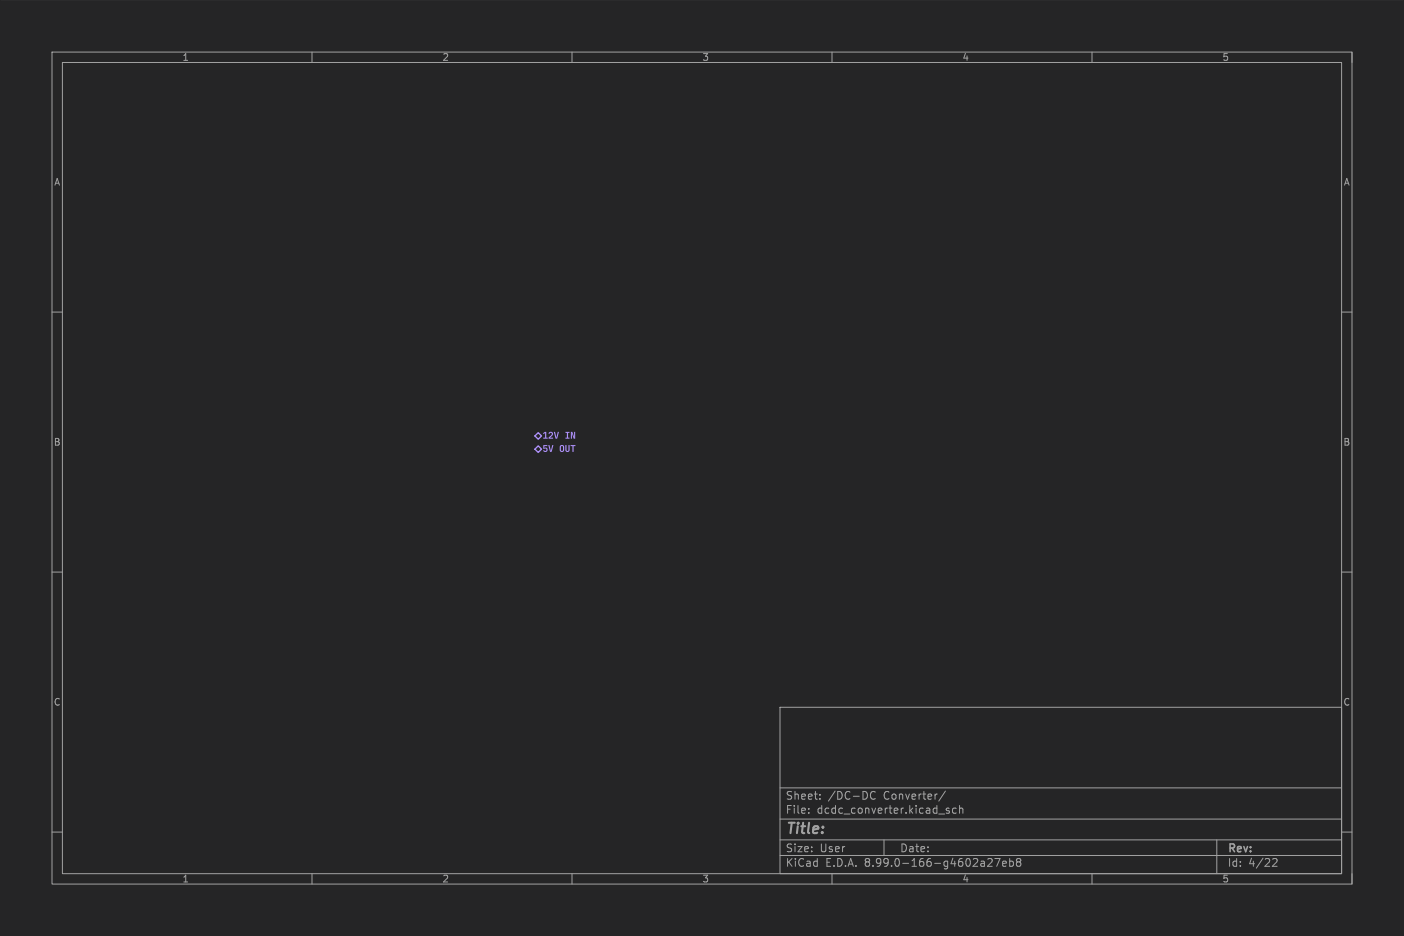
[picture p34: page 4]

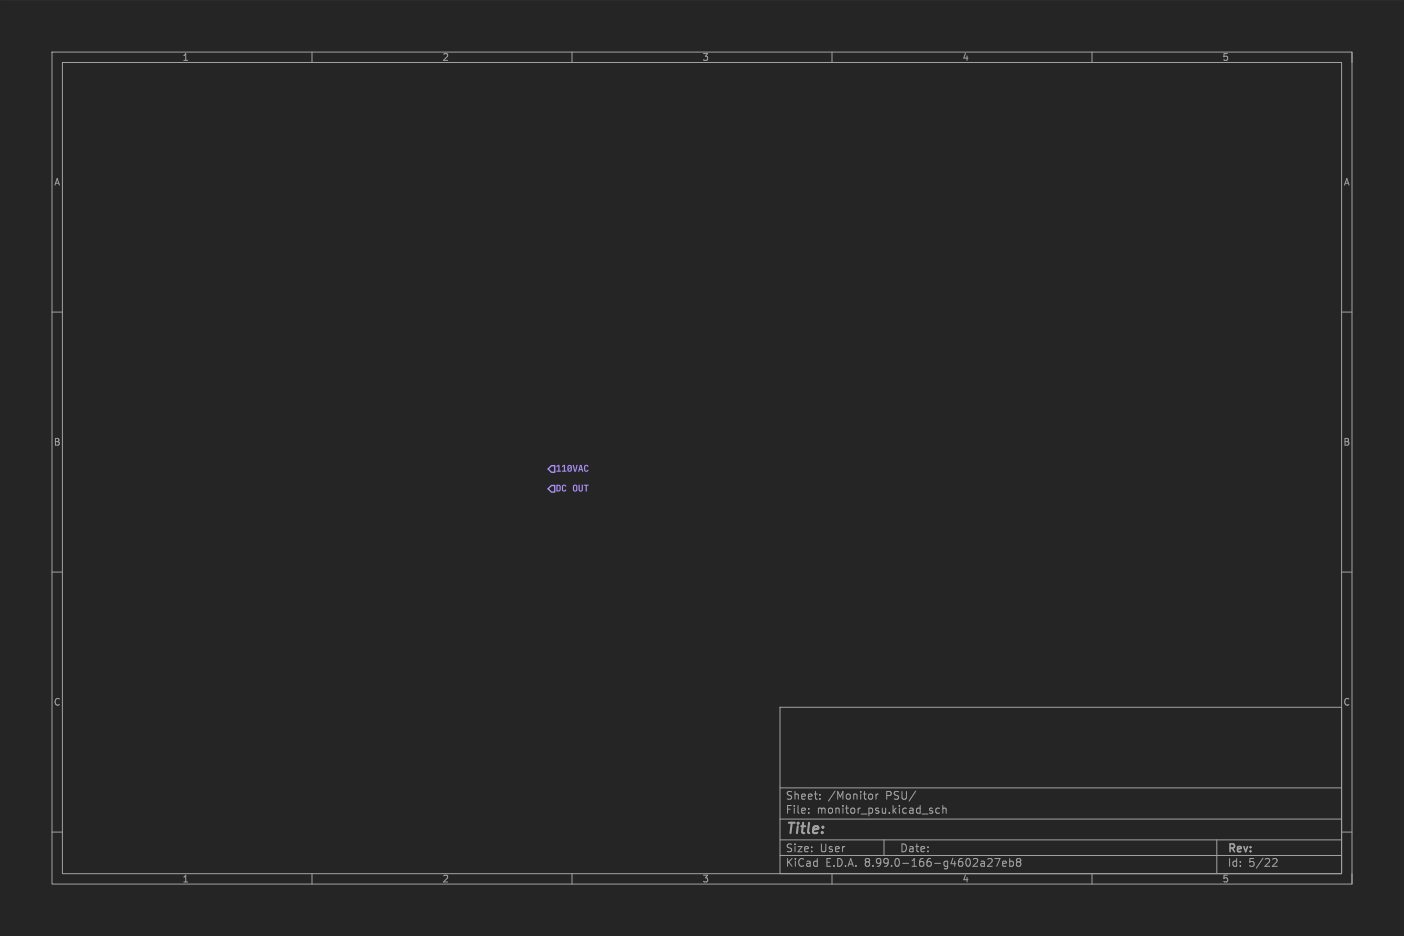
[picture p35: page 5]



Id: 7/22 Title: File: computer.kicad_sch Sheet: /Computer/ HDMI BLE WIFI DC IN


Id: 8/22 Title: File: monitor.kicad_sch Sheet: /Monitor/ HDMI DC IN












Id: 19/22 Title: File: mascp_pico.kicad_sch Sheet: /Pico/ UART PWM



Id: 21/22 Title: File: controller.kicad_sch Sheet: /Controller/ BLE


Id: 22/22 Title: File: router.kicad_sch Sheet: /Router/ PSU IN

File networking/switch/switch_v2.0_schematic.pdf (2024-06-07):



// ATTEMPT THE IMPOSSIBLE. VCC



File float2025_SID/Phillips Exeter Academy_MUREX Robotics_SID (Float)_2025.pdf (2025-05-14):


Float Full Load Amps (FLA) in water = 4.2A


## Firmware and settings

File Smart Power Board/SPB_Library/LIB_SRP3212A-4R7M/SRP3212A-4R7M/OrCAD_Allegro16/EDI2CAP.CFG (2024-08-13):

;>------- Configuration parameters: -------<
;>------Check EDIF2CAP.PDF for details ----<

[OrCAD Writer]

SuppressWarnings = 0	
ConvertOnlyLibs = 0
UnitMeasurement = default
PinToPin = 0
Grid = 0
EnableOffgridObjects = 0
GenerateIniFile = 1
OrcadConventions = 1
UseDesignatorsForPackaging = 1
DesignatorsEndOnLetters = 0
DesignatorsSameInHierarchy = 1
GeneratePinNumbers = 0
GeneratePortSymbols = 1
GenerateOffPageConnectors = 0
GenerationVisible = 1
CaptureLibsWithUserPackages = ""
SystemNetNamePrefix = ""
BackgroundTextScale = 0.8
DefaultNetNameScale = 0.3
StandardPageSize = 0
EliminatePageText = 0
SmashTitleBlock = 0
PinDisplayStyle = orcad
TopView = ""
ComponentsMode = 0
ReplacePartWithNoPinsWithTitleBlock = 0
ChangeBusBaseThatEndsOnDigit = 0
ProcessBackAnnotation = 1

[Mapper]

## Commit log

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2023-05-05 Fix: Fix ESC project layout
    [ESC.kicad_pcb, ESC.kicad_sch]
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2023-05-06 Feat: created CM4 schematic with modifications to fit needs
    [CM4_GPIO.kicad_sch, CM4_HighSpeed.kicad_sch, PCIe.kicad_sch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]
2023-05-07 Feat: added all sensors, neopixel, buzzer and usb-c to carrier board
    [CM4_GPIO.kicad_sch, CM4_HighSpeed.kicad_sch, USB2-HUB.kicad_sch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]
2023-05-07 Fix: fixed power.kicad_pro
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2023-05-07 Fix: fixed 3D models for carrier board
    [CM4_GPIO.kicad_sch, USB2-HUB.kicad_sch, carrier.kicad_pcb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]
2023-05-07 Feat: Attempted to add TPS568230 library (+ custom symbol)
    [power.kicad_sch]
2023-05-07 Fix: added footprint of TPS568230
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2023-05-07 Fix: fixed switch project
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2023-05-10 Fix: Reworked LTC4352 Symbol
    [power.kicad_sch]
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2023-05-12 Feat: matrix-based leak sensing
    [CM4_GPIO.kicad_sch, leaksensor.kicad_sch, sensors.kicad_sch]
2023-05-12 Fix: added jumpers to all i2c sensors
    [sensors.kicad_sch]
2023-05-12 Fix: minor labeling and test pad fixes
    [CM4_GPIO.kicad_sch, USB2-HUB.kicad_sch, neopixel.kicad_sch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]
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2023-05-13 Fix: renamed ESC Carrier board folder
    [ESC_Carrier.kicad_pcb, ESC_Carrier.kicad_sch]
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2023-05-14 Refactor: small changes for carrier, cm4 and leaksensors
    [CM4_GPIO.kicad_sch, carrier.kicad_sch, leaksensor.kicad_sch]
2023-05-14 Refactor/Feat: refactored projects into networking folder and created rj45_breakout project
    [plc.kicad_pcb, plc.kicad_sch, rj45_breakout.kicad_pcb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]
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2023-05-14 Fix: relinked footprints
    [USB2-HUB.kicad_sch, connectors.kicad_sch, leaksensor.kicad_sch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]
2023-05-15 Feat: Added 01x03 Conn. for Power to ESC_Carrier
    [main.kicad_sch, power.kicad_sch]
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2023-05-15 Fix: Switched hierarchical labels, added M.2 Conn.
    [power.kicad_sch]
2023-05-15 Feat: begun work on carrier pcb and imported NGFF m.2 library
    [carrier.kicad_pcb, connectors.kicad_sch, leaksensor.kicad_sch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]
2023-05-16 Feat: imported m.2 connector and more work on carrier board
    [carrier.kicad_pcb, connectors.kicad_sch]
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2023-05-16 Feat: organized PCB file, preparing for layout and routing.
    [carrier.kicad_pcb, connectors.kicad_sch, leaksensor.kicad_sch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]
2023-05-16 FEAT: finalized data pinout for esc carrier board
    [ESC_Carrier.kicad_sch]
2023-05-16 Fix: Altered M.2 Pinout
    [power.kicad_sch]
2023-05-17 Fix: Added Library M.2 Symbol
    [power.kicad_sch]
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2023-05-18 Feat: Added draft resistance and capacitance to softstarter
    [Custom_Softstarter.kicad_sch]
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2023-05-19 Fix: added rounded corners and a few minor fixes
    [carrier.kicad_pcb]
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2023-05-23 FIX: fixed crown-edge connectors on ESC Carrier
    [ESC_Carrier.kicad_sch]
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2023-05-30 Feat: power line routing, marked down necessary revisions, rerouted i2c
    [carrier.kicad_pcb, connectors.kicad_sch]
2023-05-30 Feat: most routes on i2c side and power complete
    [carrier.kicad_pcb, carrier.kicad_sch, connectors.kicad_sch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]
2023-05-30 Feat: updated efuse symbol and assigned some footprints
    [ESC_Carrier.kicad_sch]
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2023-06-04 Fix: updated esc carrier to esc connectors
    [ESC_Carrier.kicad_sch, te.kicad_sch]
2023-06-04 Feat: beginning work routing impedance matched diff pairs
    [carrier.kicad_pcb]
2023-06-04 Feat: impedanced matched traces calculations entered into net classes
    [carrier.kicad_pcb]
2023-06-04 Feat: routed differential pairs. 90 more routes to go
    [USB2-HUB.kicad_sch, carrier.kicad_pcb]
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2023-06-05 Fix: added phases to esc to esc carrier connector
    [ESC_Carrier.kicad_sch, te.kicad_sch]
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2023-06-05 Feat: updated esc to esc carrier connector, updated test points
    [ESC_Carrier.kicad_sch, te.kicad_sch]
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2023-06-05 Feat: conforms to jlc specs and (mostly) kicad DRC
    [CM4_GPIO.kicad_sch, carrier.kicad_sch, connectors.kicad_sch]
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2023-06-15 Feat: linked up majority of components to lcsc parts
    [carrier-CuBottom.gbr, carrier-CuIn1.gbr, carrier-CuIn2.gbr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]
2023-06-15 Feat: restructured lower half to fit ADC + power LEDs
    [carrier.kicad_sch, connectors.kicad_sch, leaksensor.kicad_sch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]
2023-06-16 Feat: fixes all around, refactored project and working on CM4 POS file
    [CM4_GPIO.kicad_sch, CM4_HighSpeed.kicad_sch, connectors.kicad_sch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]
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2023-06-16 Refactor: re-annotated schematic with cm4 connector POS configured
    [CM4_GPIO.kicad_sch, CM4_HighSpeed.kicad_sch, USB2-HUB.kicad_sch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]
2023-06-17 Feat: major revamps to pcb, finished bom and pos
    [CM4_GPIO.kicad_sch, CM4_HighSpeed.kicad_sch, USB2-HUB.kicad_sch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]
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2023-06-19 Feat: tidied up carrier board, added 3d models, fully prepared for production
    [CM4_GPIO.kicad_sch, CM4_HighSpeed.kicad_sch, USB2-HUB.kicad_sch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]
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2023-06-20 Feat: added routes and copper fill zones (phases not done)
    [ESC_Carrier.kicad_pcb, te.kicad_sch]
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2023-06-24 Feat: Added 282836-2 (Backup Screw Term. to Carrier)
    [power.kicad_pcb, power.kicad_sch]
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2023-06-25 Feat: cleaned up traces and zones, adjusted trace widths
    [ESC_Carrier.kicad_pcb]
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2023-06-26 Fix: Minor Schematic Changes
    [power.kicad_pcb, power.kicad_sch]
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2023-06-26 Fix: Relabelled UART to I2C
    [power.kicad_pcb, power.kicad_sch]
2023-06-26 Fix: Removed pull up resistors
    [INA226.kicad_sch, power.kicad_pcb, power.kicad_sch]
2023-06-27 Fix: changed m.2 interface from uart to i2c
    [carrier.kicad_sch, connectors.kicad_sch]
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2023-06-28 Fix: added ADC I2C address to back silk
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2023-07-03 Feat: 🎉🙏 carrier board v1 sent to production
    [carrier-CuBottom.gbr, carrier-CuIn1.gbr, carrier-CuIn2.gbr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]
2023-07-03 Fix: changed C12 silkscreen font
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2023-07-03 Feat: Deleted all traces, zones, and edge cuts
    [power.kicad_pcb]
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2023-07-04 Fix: silkscreen for connectors
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2023-07-04 Revert "Feat: added vias"
    This reverts commit d9f0b0a7b740c1a5059e2e7f1ed87a6101a3388b.
    [ESC_Carrier.kicad_pcb]
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2023-07-05 Fix: updated schematic to v1.1
    [CM4_GPIO.kicad_sch, CM4_HighSpeed.kicad_sch, USB2-HUB.kicad_sch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]
2023-07-05 Feat: switched phase connector to microfit, updated esc connector pinout, updated component layout
    [ESC_Carrier.kicad_pcb, ESC_Carrier.kicad_sch, te.kicad_sch]
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2023-07-06 Feat: Updated board constraints, fixed various violations
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2023-07-07 Feat: replaced efuse with ptc fuse
    [ESC_Carrier.kicad_sch, efuse.kicad_sch]
2023-07-10 Fix[carrier v1.2]: updated 5V zone for m.2
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2023-07-11 Feat: Changed microfit pinout, added copper zone over vin
    [power.kicad_sch]
2023-07-11 Feat: Increased voltage output to 5.1V, edited back silkscreen
    [TPS568215RNNR_1_sch.kicad_sch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]
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2023-07-12 Fix: updated uart connections to carrier board
    [ESC_Carrier.kicad_pcb, ESC_Carrier.kicad_sch]
2023-07-12 Feat: initialized rp2040 esc and 5530843-7 card edge footprint
    [rp2040_module.kicad_pcb, rp2040_module.kicad_sch]
2023-07-12 Fix: lowered height of card edge connector fp
2023-07-14 Feat: Restructured labels, fixed nmos polarity, rerouted board
    [INA226.kicad_sch, power.kicad_sch]
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2023-07-15 Feat: Switched to Molex Megafit, Rerouting, Updated Silkscreen
    [power.kicad_sch]
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2023-07-16 Fix[carrier1.2]: kicad wants rotation?
2023-07-18 Feat: switched thermistor to AS32_1R030, minor fixes
    [ESC_Carrier-CuBottom.gbr, ESC_Carrier-CuTop.gbr, ESC_Carrier-EdgeCuts.gbr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]
2023-07-19 Feat: added 12v zone, reduced size, switched mounting hole format
    [ESC_Carrier.kicad_sch]
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2023-07-20 Feat: Broke out I2C
    [power.kicad_sch]
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2023-07-29 Feat[esc]: schematic to pcb placement of B-G431B-ESC1 + RP2040
    [esc.kicad_sch, rp2040.kicad_sch, rp2040_module.kicad_pcb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]
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2023-08-03 Feat[esc_carrier 1.1]: refactored pinout to esc, made board smaller
    [ESC_Carrier.kicad_sch, te.kicad_sch]
2023-08-03 Fix: removed esc_carrier v1.0, removed blender files
    [ESC_Carrier-CuBottom.gbr, ESC_Carrier-CuTop.gbr, ESC_Carrier-EdgeCuts.gbr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]
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2023-08-31 Feat[switch]: added sheet metadata and magnetics symbols to sch
    [IP175G.kicad_sch, magnetics.kicad_sch, power.kicad_sch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]
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2023-08-31 Feat[switch]: more work on IP175G schematic, much more to be completed
    [IP175G.kicad_sch]
2023-08-31 Fix[switch]: renamed quad to dual transformer
    [magnetics.kicad_sch]
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2023-09-01 Feat[switch]: created all necessary symbols and footprints, started PCB
    [IP175G.kicad_sch, magnetics.kicad_sch, power.kicad_sch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]
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2023-09-02 Feat[anyesc]: routing complete with concerningly tight phase routing
    [anyesc.kicad_pcb]
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2023-10-07 Feat[breakouts]: Fixed listed problems with ina226 breakout
    [ina226.kicad_sch]
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2023-10-08 Feat[switch]: Fixed single transformer footprint, added 3d models
    [switch.kicad_pcb]
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2023-10-09 Revert "Feat[breakouts]: Finished PCB layout for INA226"
    This reverts commit d5cb5f566ca028d564bfbdabe353600e678628bd.
    [ina226.kicad_sch, magnetics.kicad_sch]
2023-10-09 Feat[breakouts]: Finished PCB layout for INA226, added traces
    [ina226.kicad_pcb]
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2023-10-10 Feat[breakouts]: Rearranged PCB layout for INA226, added ground layer
    [ina226.kicad_pcb, ina226.kicad_sch]
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2023-10-18 Feat[breakouts]: Moved header pins, added silk labelling, fixed 3d model?
    [ina226.kicad_pcb]
2023-10-18 Feat[breakouts]: Fixed wiring, 3d model broken
    [ina226.kicad_pcb]
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2023-10-19 Feat[breakouts]: Fixed silk, increased board size
    [ina226.kicad_pcb]
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2023-11-03 Feat[switch]: Minor fixes for tapeout
    [magnetics.kicad_sch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]
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2023-11-28 Feat[breakouts]: Fixed some ToDOs
    [ADC.kicad_sch]
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2023-11-29 Fix[carrier]: switch bmi088 to i2c mode
    [sensors.kicad_sch]
2023-11-29 Fix[carrier]: added bmi088 i2c addresses
    [sensors.kicad_sch]
2023-11-29 Fix[carrier]: current adjustments
    [power.kicad_sch]
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2023-12-02 Fix[esc carrier]: fixed 3d models
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2023-12-11 Fix[carrier]: fix i2c pull up resistor jlc mapping
2023-12-31 Fix: updated carrier board to v3.1
    [CM4_GPIO.kicad_sch, CM4_HighSpeed.kicad_sch, USB2.kicad_sch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]
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2024-02-11 Fix: added esc carrier back
    [ESC_Carrier-CuBottom.gbr, ESC_Carrier-CuTop.gbr, ESC_Carrier-EdgeCuts.gbr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]
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2024-03-07 Fix: revised shield schematic and pcb
    [shield.kicad_pcb, shield.kicad_sch]
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2024-03-09 Fix: fixed some labels
    [shield.kicad_pcb]
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2024-04-04 Fix: panelized shield
    [shield.kicad_pcb, shield.kicad_sch]
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2024-06-23 Fix link to network switch docs
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2024-10-13 Feat[shield]: board layout and schem fixes
    [shield.kicad_pcb, shield.kicad_sch]
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2024-10-23 Fix[electrical]: resolve 8.99 pcb_text crash
    [RP2040.kicad_sch, minifoc esc.kicad_pcb]
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2024-12-14 Feat[SmartPowerBoard]: Fixing Layout
    [SmartPowerBoard.kicad_pcb]
2024-12-14 Feat[SmartPowerBoard]: DRC Errors Fixed
    [SmartPowerBoard.kicad_pcb]
2024-12-15 Feat[SmartPowerBoard]: Vias fixed
    [SmartPowerBoard.kicad_pcb]
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2025-07-16 Fix: remove bom/cpl from gitignore
    [BOM-anyesc.csv, BOM-minifoc esc.csv, BOM-shield.csv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]
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2025-12-25 Feat[float_carrier_2025-2026]:connectors 3D symbol fixed, edge cut fixed
    [float_carrier_2025-2026.kicad_pcb, float_carrier_2025-2026.kicad_sch, untitled.kicad_sch]
2026-01-02 Feat[float_carrier_2025-2026]: silkscreen added, connectors and inductor changed, gerber file and BOM file made
    [BOM-float_carrier_2025-2026.csv, bom.csv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]
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2026-03-16 Feat[Fatpower]: Add 3.3V Buck Schematic, Vin/Vout pin of buck fixed, power connectors of navigator board/ethernet switch added
    [3.3VBuck.kicad_sch, 5VBuck.kicad_sch, fatpower.kicad_sch]
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
